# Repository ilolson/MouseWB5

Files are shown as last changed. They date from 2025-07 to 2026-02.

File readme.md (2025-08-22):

# MouseWB5 
40mm x 65.5mm Mini RC car inspired by half size micro mouse.
It is powered by the STM32WB5 precertified wireless module.
It uses STSPIN240 motor drivers to power four small coreless DC motors.
Contains the LSM6DSO as an IMU, and has headers for an additional fan motor for a suction mechanism.
SPI and I2C module connections for future VL53 lidar sensors, as well as programmable drift lights and turn signals. 
Includes a battery charging circuit and can be programmed via the TC2030 debug connector.
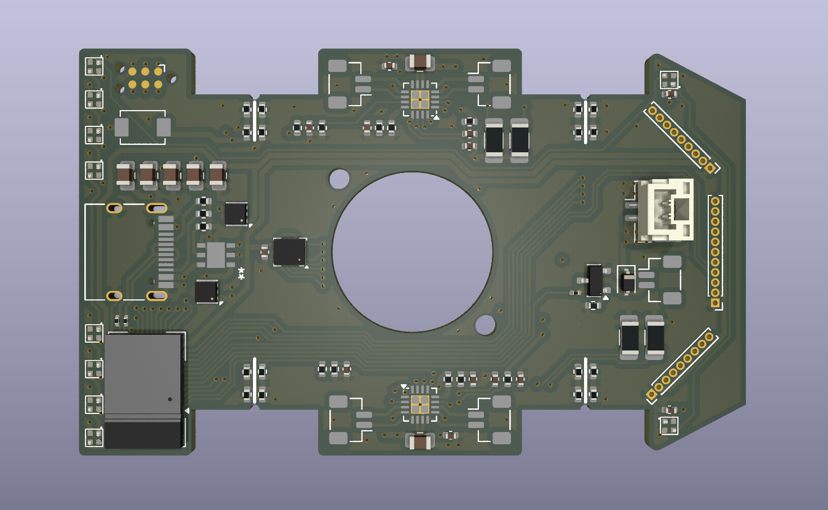
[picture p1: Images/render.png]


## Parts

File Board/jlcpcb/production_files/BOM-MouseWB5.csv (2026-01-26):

Comment | Designator | Footprint | LCSC | Quantity
100n | C19,C2,C20 | C_0402_1005Metric | C1525 | 3
10nF | C13,C14 | C_0402_1005Metric | C15195 | 2
10u | C1,C10,C21,C22,C4,C5,C7 | C_0805_2012Metric | C408141 | 7
11k | R22,R23 | R_0402_1005Metric | C25749 | 2
1N5819WS | D4 | D_SOD-323 | C191023 | 1
1k | R7,R8 | R_0402_1005Metric | C106235 | 2
1nF | C15,C16 | C_0402_1005Metric | C77018 | 2
2.2uf | C11,C12 | C_0402_1005Metric | C170151 | 2
20k | R11,R19,R20,R3,R4,R9 | R_0402_1005Metric | C93942 | 6
22k | R21,R24 | R_0402_1005Metric | C82868 | 2
22nF | C8,C9 | C_0402_1005Metric | C337699 | 2
22r | R18,R5,R6 | R_0201_0603Metric | C270355 | 3
22uF | C3,C6 | C_0805_2012Metric | C602037 | 2
2k | R10 | R_0402_1005Metric | C4109 | 1
330mR | R14,R15,R16,R17 | R_1206_3216Metric_Pad1.30x1.75mm_HandSolder | C2932844 | 4
47k | R12,R13 | R_0402_1005Metric | C93943 | 2
47nF | C17,C18 | C_0402_1005Metric | C82219 | 2
5.1k | MR1,MR10,MR11,MR12,MR13,MR14,MR15,MR16,MR2,MR3,MR4,MR5,MR6,MR7,MR8,MR9,R1,R2 | R_0402_1005Metric | C105872 | 18
Conn_01x02_Socket | J9,M1,M2,M3,M4,M5 | JST_GH_BM02B-GHS-TBT_1x02-1MP_P1.25mm_Vertical | C161690 | 6
LP5912-1.8DRV | U4 | WSON-6-1EP_2x2mm_P0.65mm_EP1x1.6mm_ThermalVias | C2876234 | 1
LP5912-3.3DRV | U7 | WSON-6-1EP_2x2mm_P0.65mm_EP1x1.6mm_ThermalVias | C524780 | 1
LSM6DS0 | U5 | LGA-14_3x2.5mm_P0.5mm_LayoutBorder3x4y | C481766 | 1
MCC SI8810 | Q2 | SOT-23 | C669009 | 1
STBC08PMR | U6 | DFN6_3X3_STM | C262929 | 1
STM32WB5MMG | U1 | ST-SiP-LGA-86-11x7.3mm | C5184586 | 1
STSPIN240 | U2,U3 | VQFN-16-1EP_3x3mm_P0.5mm_EP1.8x1.8mm | C962258 | 2
SW_Push | SW1 | TS-1088-AR02016 | C455280 | 1
USB_C_Receptacle_USB2.0_14P | J1 | USB_C_Receptacle_HRO_TYPE-C-31-M-12 | C165948 | 1
WS2812B | LED1,LED10,LED2,LED3,LED4,LED5,LED6,LED7,LED8,LED9 | LED-SMD_4P-L1.0-W1.0-TL_XL-1010RGBC-WS2812B | C5349953 | 10

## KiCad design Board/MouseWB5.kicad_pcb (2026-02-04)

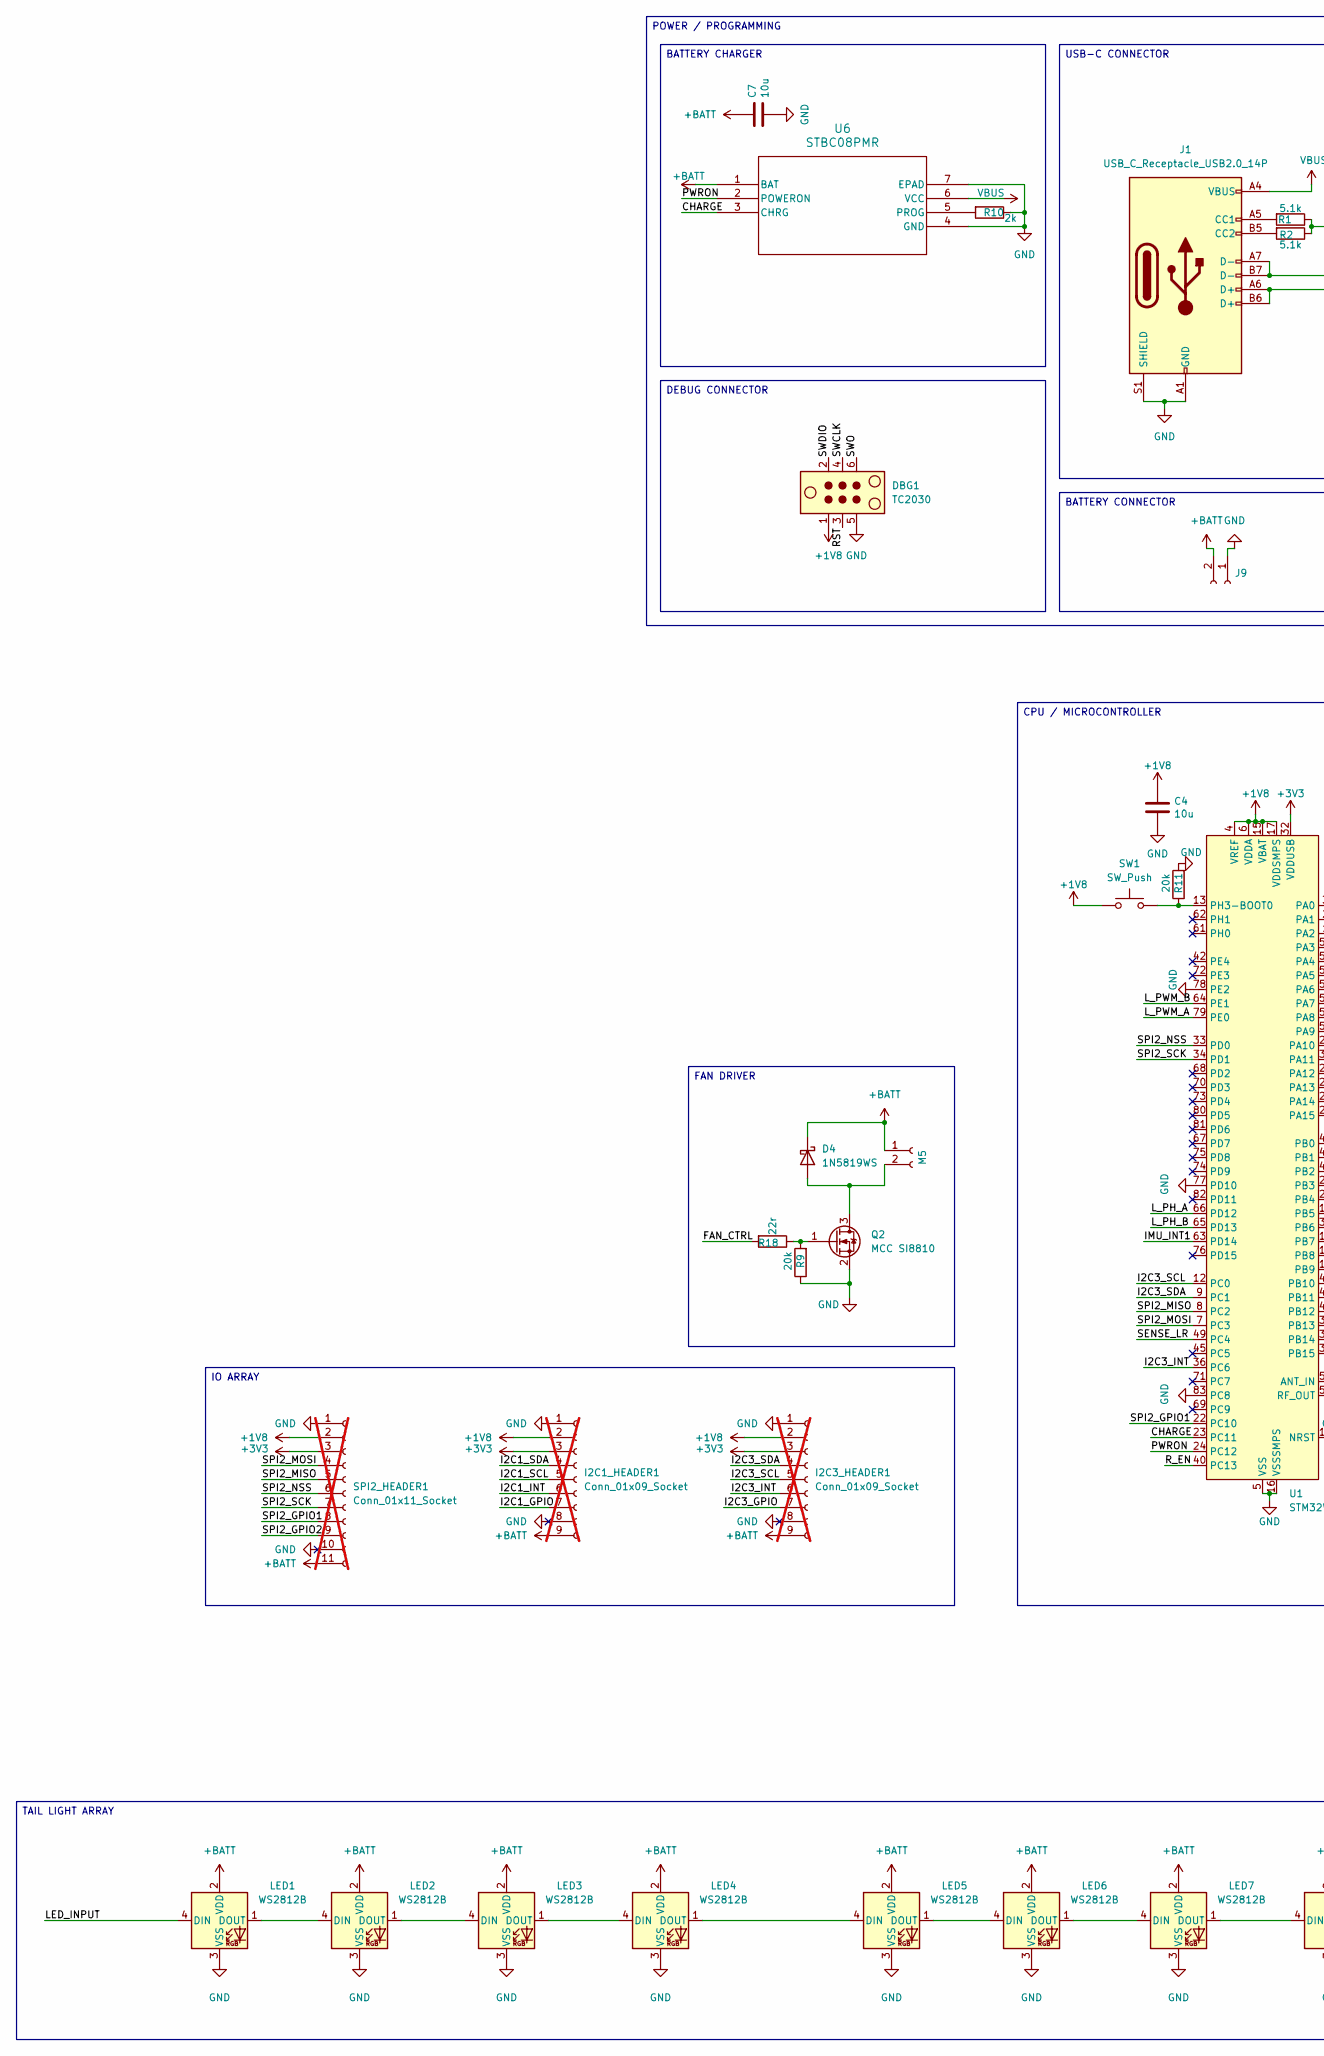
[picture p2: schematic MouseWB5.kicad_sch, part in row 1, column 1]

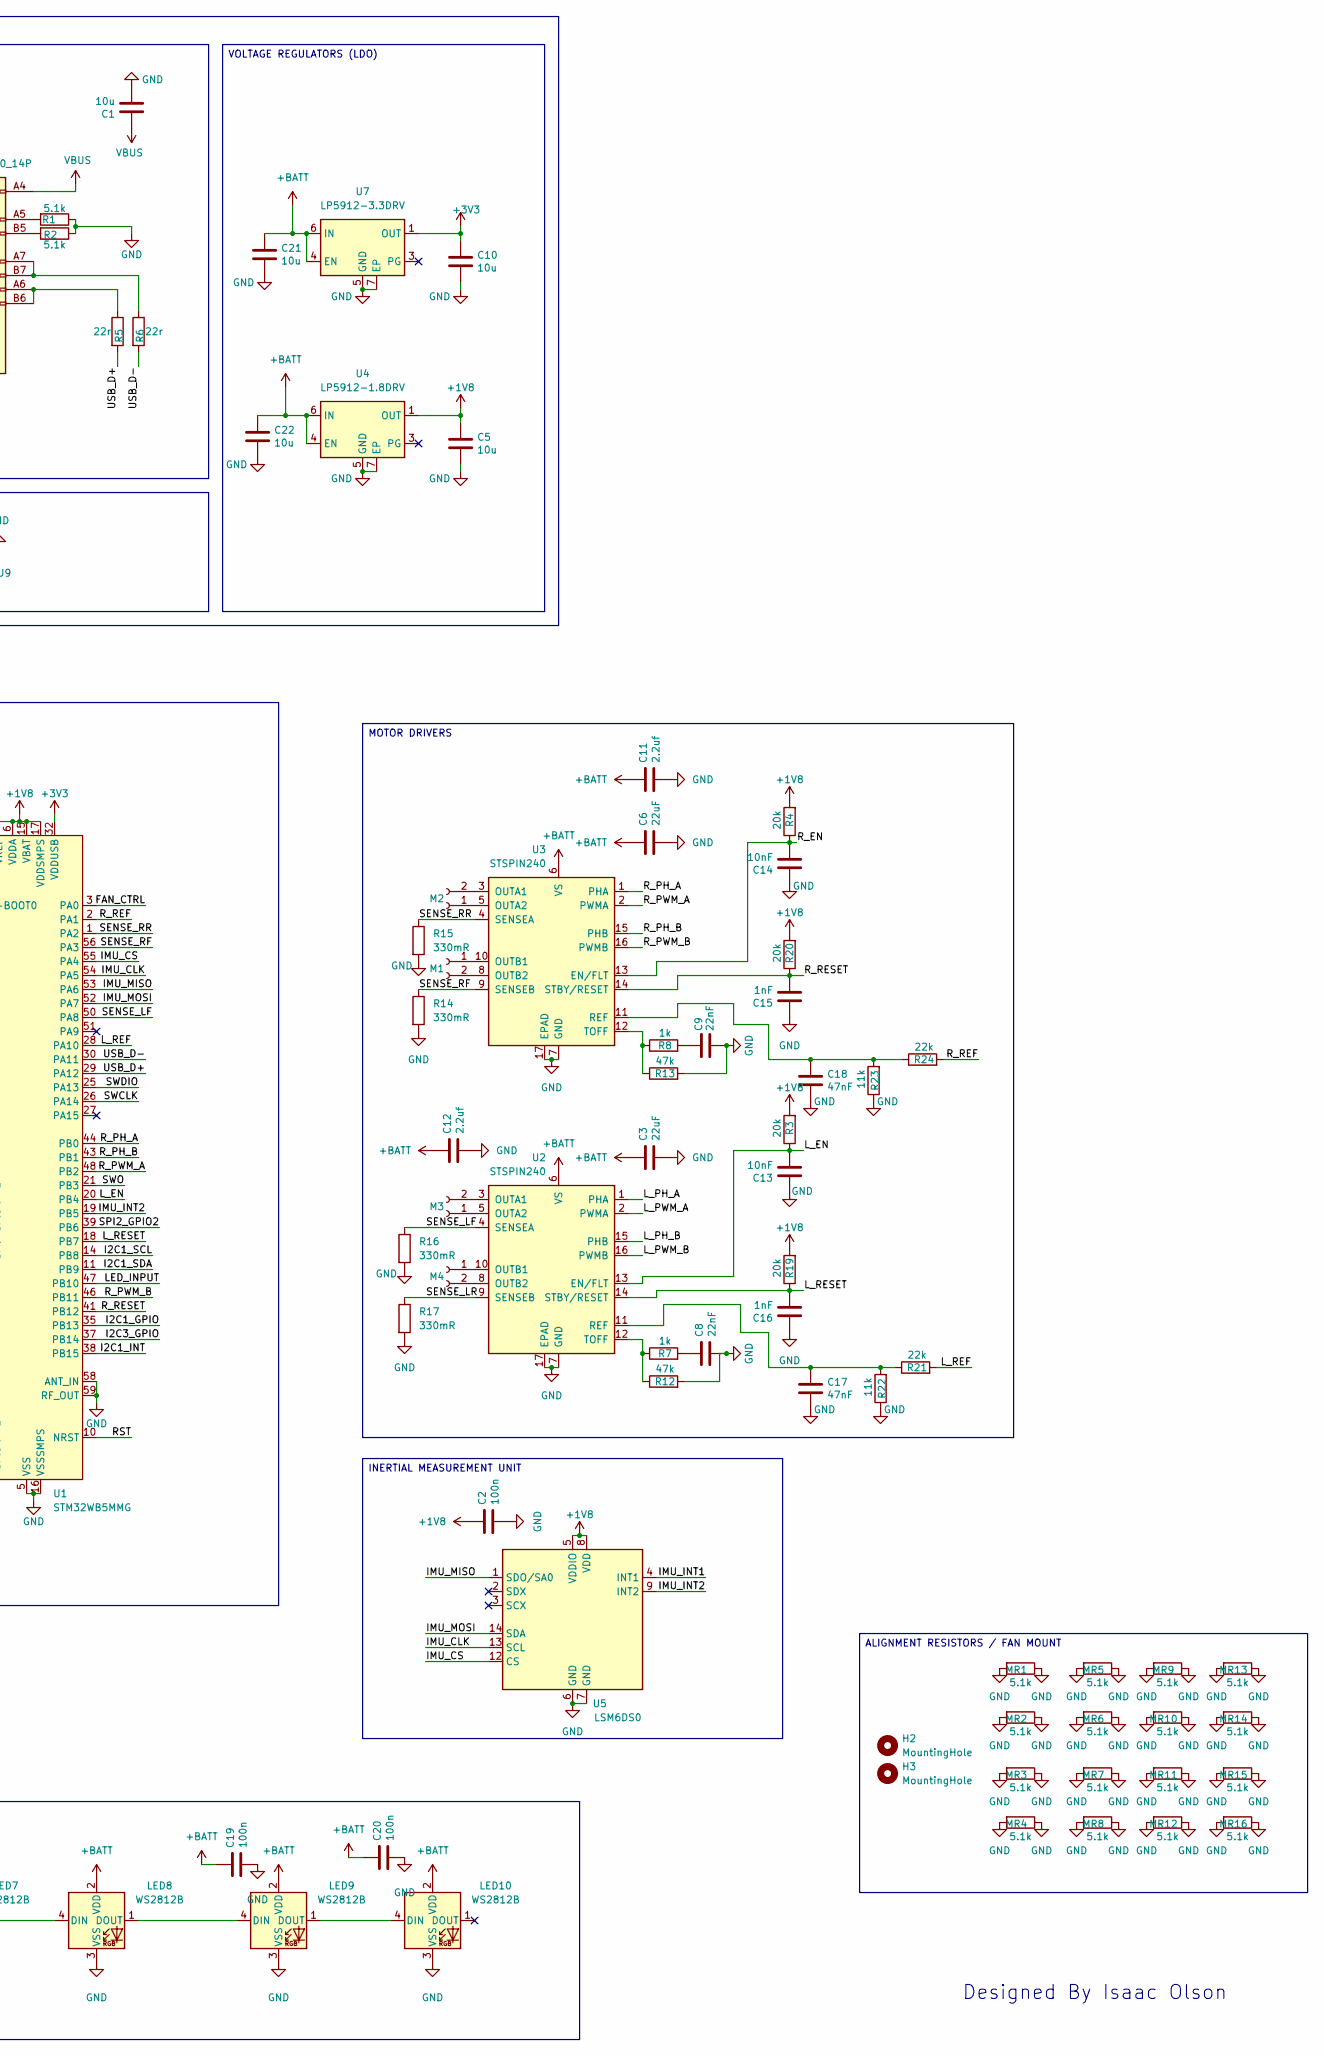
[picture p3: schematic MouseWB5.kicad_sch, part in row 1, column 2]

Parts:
C1, C4, C5, C7, C10, C21, C22: 10u; C_0805_2012Metric; LCSC C408141
C2, C19, C20: 100n; C_0402_1005Metric; LCSC C1525
C3, C6: 22uF; C_0805_2012Metric; LCSC C602037
C8, C9: 22nF; C_0402_1005Metric; LCSC C337699
C11, C12: 2.2uf; C_0402_1005Metric; LCSC C170151
C13, C14: 10nF; C_0402_1005Metric; LCSC C15195
C15, C16: 1nF; C_0402_1005Metric; LCSC C77018
C17, C18: 47nF; C_0402_1005Metric; LCSC C82219
D4: 1N5819WS; D_SOD-323; LCSC C191023
DBG1: TC2030; Tag-Connect_TC2030-IDC-NL_2x03_P1.27mm_Vertical
H2, H3: MountingHole; MountingHole_2.1mm
I2C1_HEADER1, I2C3_HEADER1: Conn_01x09_Socket; PinHeader_1x09_P1.00mm_Vertical; not fitted
J1: USB_C_Receptacle_USB2.0_14P; USB_C_Receptacle_HRO_TYPE-C-31-M-12; LCSC C165948
J9: Conn_01x02_Socket; JST_GH_BM02B-GHS-TBT_1x02-1MP_P1.25mm_Vertical; LCSC C161690
LED1, LED2, LED3, LED4, LED5, LED6, LED7, LED8: WS2812B; LED-SMD_4P-L1.0-W1.0-TL_XL-1010RGBC-WS2812B; LCSC C5349953
LED9, LED10: WS2812B; 1010ws2812; LCSC C5349953
M1, M2, M3, M4, M5: Conn_01x02_Socket; JST_GH_BM02B-GHS-TBT_1x02-1MP_P1.25mm_Vertical; LCSC C161690
MR1, MR2, MR3, MR4, MR5, MR6, MR7, MR8, MR9, MR10, MR11, MR12, MR13, MR14, MR15, MR16: 5.1k; R_0402_1005Metric; LCSC C105872
Q2: MCC SI8810; SOT-23; LCSC C669009
R1, R2: 5.1k; R_0402_1005Metric; LCSC C105872
R3, R4, R9, R11, R19, R20: 20k; R_0402_1005Metric; LCSC C93942
R5, R6, R18: 22r; R_0201_0603Metric; LCSC C270355
R7, R8: 1k; R_0402_1005Metric; LCSC C106235
R10: 2k; R_0402_1005Metric; LCSC C4109
R12, R13: 47k; R_0402_1005Metric; LCSC C93943
R14, R15, R16, R17: 330mR; R_1206_3216Metric_Pad1.30x1.75mm_HandSolder; LCSC C2932844
R21, R24: 22k; R_0402_1005Metric; LCSC C82868
R22, R23: 11k; R_0402_1005Metric; LCSC C25749
SPI2_HEADER1: Conn_01x11_Socket; PinHeader_1x11_P1.00mm_Vertical; not fitted
SW1: SW_Push; TS-1088-AR02016; LCSC C455280
U1: STM32WB5MMG; ST-SiP-LGA-86-11x7.3mm; LCSC C5184586
U2, U3: STSPIN240; VQFN-16-1EP_3x3mm_P0.5mm_EP1.8x1.8mm; LCSC C962258
U4: LP5912-1.8DRV; WSON-6-1EP_2x2mm_P0.65mm_EP1x1.6mm_ThermalVias; LCSC C2876234
U5: LSM6DS0; LGA-14_3x2.5mm_P0.5mm_LayoutBorder3x4y; LCSC C481766
U6: STBC08PMR; DFN6_3X3_STM; LCSC C262929
U7: LP5912-3.3DRV; WSON-6-1EP_2x2mm_P0.65mm_EP1x1.6mm_ThermalVias; LCSC C524780

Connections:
+1V8: C2.1, C4.1, C5.1, DBG1.1, I2C1_HEADER1.2, I2C3_HEADER1.2, R3.2, R4.2, R19.2, R20.2, SPI2_HEADER1.2, SW1.1, U1.4 (VREF), U1.6 (VDDA), U1.15 (VBAT), U1.17 (VDDSMPS), U4.1 (OUT), U5.5 (VDDIO), U5.8 (VDD)
+3V3: C10.1, I2C1_HEADER1.3, I2C3_HEADER1.3, SPI2_HEADER1.3, U1.32 (VDDUSB), U7.1 (OUT)
+BATT: C3.1, C6.1, C7.1, C11.1, C12.1, C19.1, C20.1, C21.1, C22.1, D4.1 (K), I2C1_HEADER1.9, I2C3_HEADER1.9, J9.2, LED1.2 (VDD), LED2.2 (VDD), LED3.2 (VDD), LED4.2 (VDD), LED5.2 (VDD), LED6.2 (VDD), LED7.2 (VDD), LED8.2 (VDD), LED9.2 (VDD), LED10.2 (VDD), M5.1, SPI2_HEADER1.11, U2.6 (VS), U3.6 (VS), U4.4 (EN), U4.6 (IN), U6.1 (BAT), U7.4 (EN), U7.6 (IN)
/CHARGE: U1.23 (PC11), U6.3 (CHRG)
/FAN_CTRL: R18.2, U1.3 (PA0)
/I2C1_GPIO: I2C1_HEADER1.7, U1.35 (PB13)
/I2C1_INT: I2C1_HEADER1.6, U1.38 (PB15)
/I2C1_SCL: I2C1_HEADER1.5, U1.14 (PB8)
/I2C1_SDA: I2C1_HEADER1.4, U1.11 (PB9)
/I2C3_GPIO: I2C3_HEADER1.7, U1.37 (PB14)
/I2C3_INT: I2C3_HEADER1.6, U1.36 (PC6)
/I2C3_SCL: I2C3_HEADER1.5, U1.12 (PC0)
/I2C3_SDA: I2C3_HEADER1.4, U1.9 (PC1)
/IMU_CLK: U1.54 (PA5), U5.13 (SCL)
/IMU_CS: U1.55 (PA4), U5.12 (CS)
/IMU_INT1: U1.63 (PD14), U5.4 (INT1)
/IMU_INT2: U1.19 (PB5), U5.9 (INT2)
/IMU_MISO: U1.53 (PA6), U5.1 (SDO/SA0)
/IMU_MOSI: U1.52 (PA7), U5.14 (SDA)
/LED_INPUT: LED1.4 (DIN), U1.47 (PB10)
/L_EN: C13.2, R3.1, U1.20 (PB4), U2.13 (EN/FLT)
/L_PH_A: U1.66 (PD12), U2.1 (PHA)
/L_PH_B: U1.65 (PD13), U2.15 (PHB)
/L_PWM_A: U1.79 (PE0), U2.2 (PWMA)
/L_PWM_B: U1.64 (PE1), U2.16 (PWMB)
/L_REF: R21.2, U1.28 (PA10)
/L_RESET: C16.2, R19.1, U1.18 (PB7), U2.14 (STBY/RESET)
/PWRON: U1.24 (PC12), U6.2 (POWERON)
/RST: DBG1.3, U1.10 (NRST)
/R_EN: C14.2, R4.1, U1.40 (PC13), U3.13 (EN/FLT)
/R_PH_A: U1.44 (PB0), U3.1 (PHA)
/R_PH_B: U1.43 (PB1), U3.15 (PHB)
/R_PWM_A: U1.48 (PB2), U3.2 (PWMA)
/R_PWM_B: U1.46 (PB11), U3.16 (PWMB)
/R_REF: R24.2, U1.2 (PA1)
/R_RESET: C15.2, R20.1, U1.41 (PB12), U3.14 (STBY/RESET)
/SENSE_LF: R16.1, U1.50 (PA8), U2.4 (SENSEA)
/SENSE_LR: R17.1, U1.49 (PC4), U2.9 (SENSEB)
/SENSE_RF: R14.1, U1.56 (PA3), U3.9 (SENSEB)
/SENSE_RR: R15.1, U1.1 (PA2), U3.4 (SENSEA)
/SPI2_GPIO1: SPI2_HEADER1.8, U1.22 (PC10)
/SPI2_GPIO2: SPI2_HEADER1.9, U1.39 (PB6)
/SPI2_MISO: SPI2_HEADER1.5, U1.8 (PC2)
/SPI2_MOSI: SPI2_HEADER1.4, U1.7 (PC3)
/SPI2_NSS: SPI2_HEADER1.6, U1.33 (PD0)
/SPI2_SCK: SPI2_HEADER1.7, U1.34 (PD1)
/SWCLK: DBG1.4, U1.26 (PA14)
/SWDIO: DBG1.2, U1.25 (PA13)
/SWO: DBG1.6, U1.21 (PB3)
/USB_D+: R5.2, U1.29 (PA12)
/USB_D-: R6.2, U1.30 (PA11)
GND: C1.2, C2.2, C3.2, C4.2, C5.2, C6.2, C7.2, C8.2, C9.2, C10.2, C11.2, C12.2, C13.1, C14.1, C15.1, C16.1, C17.2, C18.2, C19.2, C20.2, C21.2, C22.2, DBG1.5, I2C1_HEADER1.1, I2C1_HEADER1.8, I2C3_HEADER1.1, I2C3_HEADER1.8, J1.A1 (GND), J1.A12 (GND), J1.B1 (GND), J1.B12 (GND), J1.S1 (SHIELD), J9.1, LED1.3 (VSS), LED2.3 (VSS), LED3.3 (VSS), LED4.3 (VSS), LED5.3 (VSS), LED6.3 (VSS), LED7.3 (VSS), LED8.3 (VSS), LED9.3 (VSS), LED10.3 (VSS), MR1.1, MR1.2, MR2.1, MR2.2, MR3.1, MR3.2, MR4.1, MR4.2, MR5.1, MR5.2, MR6.1, MR6.2, MR7.1, MR7.2, MR8.1, MR8.2, MR9.1, MR9.2, MR10.1, MR10.2, MR11.1, MR11.2, MR12.1, MR12.2, MR13.1, MR13.2, MR14.1, MR14.2, MR15.1, MR15.2, MR16.1, MR16.2, Q2.2 (S), R1.1, R2.1, R9.1, R10.1, R11.2, R12.2, R13.2, R14.2, R15.2, R16.2, R17.2, R22.1, R23.1, SPI2_HEADER1.1, SPI2_HEADER1.10, U1.5 (VSS), U1.16 (VSSSMPS), U1.31 (VSS), U1.57 (VSS), U1.58 (ANT_IN), U1.59 (RF_OUT), U1.60 (VSS), U1.77 (PD10), U1.78 (PE2), U1.83 (PC8), U1.84 (VSS), U1.86 (VSS), U2.7 (GND), U2.17 (EPAD), U3.7 (GND), U3.17 (EPAD), U4.5 (GND), U4.7 (EP), U5.6 (GND), U5.7 (GND), U6.4 (GND), U6.7 (EPAD), U7.5 (GND), U7.7 (EP)
unnamed: C8.1, R7.2
unnamed: C9.1, R8.2
unnamed: D4.2 (A), M5.2, Q2.3 (D)
unnamed: J1.A5 (CC1), R1.2
unnamed: J1.B5 (CC2), R2.2
unnamed: J1.A6 (D+), J1.B6 (D+), R5.1
unnamed: J1.A7 (D-), J1.B7 (D-), R6.1
unnamed: LED1.1 (DOUT), LED2.4 (DIN)
unnamed: LED2.1 (DOUT), LED3.4 (DIN)
unnamed: LED3.1 (DOUT), LED4.4 (DIN)
unnamed: LED4.1 (DOUT), LED5.4 (DIN)
unnamed: LED5.1 (DOUT), LED6.4 (DIN)
unnamed: LED6.1 (DOUT), LED7.4 (DIN)
unnamed: LED7.1 (DOUT), LED8.4 (DIN)
unnamed: LED8.1 (DOUT), LED9.4 (DIN)
unnamed: LED9.1 (DOUT), LED10.4 (DIN)
unnamed: M1.1, U3.10 (OUTB1)
unnamed: M1.2, U3.8 (OUTB2)
unnamed: M2.1, U3.5 (OUTA2)
unnamed: M2.2, U3.3 (OUTA1)
unnamed: M3.1, U2.5 (OUTA2)
unnamed: M3.2, U2.3 (OUTA1)
unnamed: M4.1, U2.10 (OUTB1)
unnamed: M4.2, U2.8 (OUTB2)
unnamed: Q2.1 (G), R9.2, R18.1
unnamed: R11.1, SW1.2, U1.13 (PH3-BOOT0)
unnamed: C17.1, R21.1, R22.2, U2.11 (REF)
unnamed: R7.1, R12.1, U2.12 (TOFF)
unnamed: C18.1, R23.2, R24.1, U3.11 (REF)
unnamed: R8.1, R13.1, U3.12 (TOFF)
unnamed: R10.2, U6.5 (PROG)
VBUS: C1.1, J1.A4 (VBUS), J1.A9 (VBUS), J1.B4 (VBUS), J1.B9 (VBUS), U6.6 (VCC)

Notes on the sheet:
Designed By Isaac Olson
ALIGNMENT RESISTORS / FAN MOUNT
MOTOR DRIVERS
CPU / MICROCONTROLLER
INERTIAL MEASUREMENT UNIT
VOLTAGE REGULATORS (LDO)
POWER / PROGRAMMING
BATTERY CONNECTOR
USB-C CONNECTOR
TAIL LIGHT ARRAY
BATTERY CHARGER
FAN DRIVER
IO ARRAY
DEBUG CONNECTOR

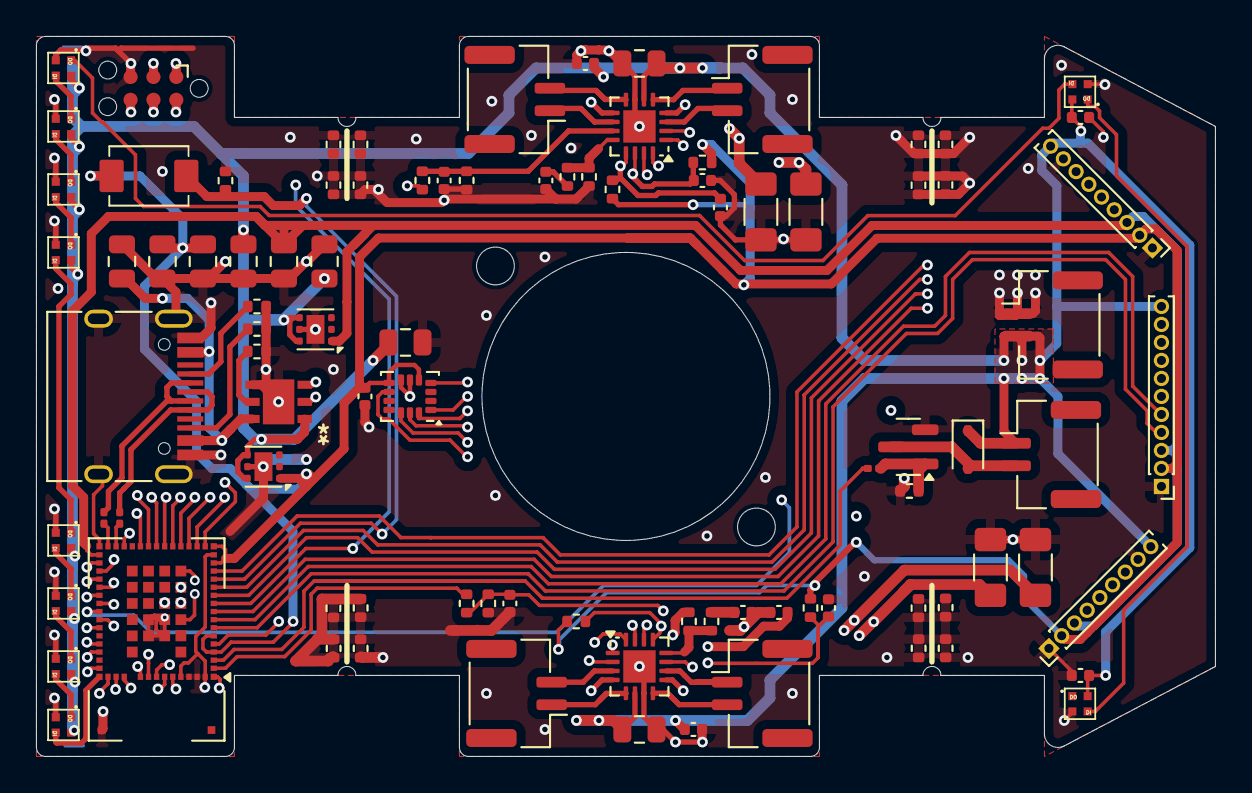
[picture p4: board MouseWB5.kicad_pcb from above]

Board: 6 copper layers, 65.5 x 40.0 mm, 95 parts (0 on the bottom side), 84 nets.

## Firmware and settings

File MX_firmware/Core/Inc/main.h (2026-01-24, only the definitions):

#define SENSE_RR_Pin GPIO_PIN_2
#define SENSE_RR_GPIO_Port GPIOA
#define R_REF_Pin GPIO_PIN_1
#define R_REF_GPIO_Port GPIOA
#define FAN_CTRL_Pin GPIO_PIN_0
#define FAN_CTRL_GPIO_Port GPIOA
#define BOOT_Pin GPIO_PIN_3
#define BOOT_GPIO_Port GPIOH
#define L_RESET_Pin GPIO_PIN_7
#define L_RESET_GPIO_Port GPIOB
#define IMU_INT1_Pin GPIO_PIN_5
#define IMU_INT1_GPIO_Port GPIOB
#define L_EN_Pin GPIO_PIN_4
#define L_EN_GPIO_Port GPIOB
#define SWO_Pin GPIO_PIN_3
#define SWO_GPIO_Port GPIOB
#define CHARGE_Pin GPIO_PIN_11
#define CHARGE_GPIO_Port GPIOC
#define PWRON_Pin GPIO_PIN_12
#define PWRON_GPIO_Port GPIOC
#define SWDIO_Pin GPIO_PIN_13
#define SWDIO_GPIO_Port GPIOA
#define SWCLK_Pin GPIO_PIN_14
#define SWCLK_GPIO_Port GPIOA
#define L_REF_Pin GPIO_PIN_10
#define L_REF_GPIO_Port GPIOA
#define TURN_L_Pin GPIO_PIN_13
#define TURN_L_GPIO_Port GPIOB
#define I2C3_INT_Pin GPIO_PIN_6
#define I2C3_INT_GPIO_Port GPIOC
#define TURN_R_Pin GPIO_PIN_14
#define TURN_R_GPIO_Port GPIOB
#define I2C1_INT_Pin GPIO_PIN_15
#define I2C1_INT_GPIO_Port GPIOB
#define SPI2_GPIO2_Pin GPIO_PIN_6
#define SPI2_GPIO2_GPIO_Port GPIOB
#define R_EN_Pin GPIO_PIN_13
#define R_EN_GPIO_Port GPIOC
#define R_RESET_Pin GPIO_PIN_12
#define R_RESET_GPIO_Port GPIOB
#define R_PH_B_Pin GPIO_PIN_1
#define R_PH_B_GPIO_Port GPIOB
#define R_PH_A_Pin GPIO_PIN_0
#define R_PH_A_GPIO_Port GPIOB
#define R_PWM_B_Pin GPIO_PIN_11
#define R_PWM_B_GPIO_Port GPIOB
#define WS2812_LED_Pin GPIO_PIN_10
#define WS2812_LED_GPIO_Port GPIOB
#define R_PWM_A_Pin GPIO_PIN_2
#define R_PWM_A_GPIO_Port GPIOB
#define SENSE_LR_Pin GPIO_PIN_4
#define SENSE_LR_GPIO_Port GPIOC
#define SENSE_LF_Pin GPIO_PIN_8
#define SENSE_LF_GPIO_Port GPIOA
#define SENSE_RF_Pin GPIO_PIN_3
#define SENSE_RF_GPIO_Port GPIOA
#define IMU_INT1D14_Pin GPIO_PIN_14
#define IMU_INT1D14_GPIO_Port GPIOD
#define L_PWM_B_Pin GPIO_PIN_1
#define L_PWM_B_GPIO_Port GPIOE
#define L_PH_B_Pin GPIO_PIN_13
#define L_PH_B_GPIO_Port GPIOD
#define L_PH_A_Pin GPIO_PIN_12
#define L_PH_A_GPIO_Port GPIOD
#define L_PWM_A_Pin GPIO_PIN_0
#define L_PWM_A_GPIO_Port GPIOE

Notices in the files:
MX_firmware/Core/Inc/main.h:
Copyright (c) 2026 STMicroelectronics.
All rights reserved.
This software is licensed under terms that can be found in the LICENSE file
